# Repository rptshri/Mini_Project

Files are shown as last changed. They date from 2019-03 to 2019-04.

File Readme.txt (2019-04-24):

http://www.me.umn.edu/education/undergraduate/writing/How-to-write-a-Design-Report.pdf

ARDUINO DESIGN:
https://www.allaboutcircuits.com/technical-articles/understanding-arduino-uno-hardware-design/

SG90 http://www.ee.ic.ac.uk/pcheung/teaching/DE1_EE/stores/sg90_datasheet.pdf

MG995 https://www.towerpro.com.tw/product/mg995/

BLUETOOTH MODULE  https://howtomechatronics.com/tutorials/arduino/arduino-and-hc-05-bluetooth-module-tutorial/

MDF https://en.wikipedia.org/wiki/Medium-density_fibreboard

3D Design https://www.tinkercad.com/things/dJmnHaHhOIF-grand-snaget-amur/edit

Materials https://www.3dhubs.com/knowledge-base/pla-vs-abs-whats-difference 

MDF Plywood difference https://www.livspace.com/magazine/mdf-vs-plywood-comparison/

1. Project report *
2. Imperial Sheet *
3. Project hardware  *   
4. Project log book *
5. altium pcb file 
6. Proteus simulation file *
7. Pcb vs schematic.  8.Code

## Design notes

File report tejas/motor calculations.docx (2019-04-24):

Mass of robot = 1.5 KG

Radius of wheel = 5.5 cm = 0.055 m

Torque required = m*g*R

Where -

m= mass of robot

G= gravity

R=radius of wheel

Therefore

Torque = 1.5*9.8*0.055

=0.8085 N.M

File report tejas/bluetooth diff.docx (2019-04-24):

parameter | Hc-05 | Hc10
Bluetooth version | BLE 2.0/3.0 | BLE4.0
Power consumption | Low | Very Low
cost | Rs 283 /- | Rs 342 /-

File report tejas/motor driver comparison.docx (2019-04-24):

MOTOR DRIVER COMPARISON

Parameter | L293d | L298n
Circuit | Quadruple half bridge | Dual full H bridge
Supply voltage range | 4.5-36v | Upto 46 v
Output current | 600 mA | 2 A
Noise immunity | High | High
Over-temperature protection | NO | YES
Internal ESD protection | YES | NO
Cost | Low | Comparatively cost
Current Sense | No | Yes

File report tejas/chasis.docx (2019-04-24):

Chasis

Chasis is internal vehicle frame that provides base and supports an artificial object in its construction and use ,it also provides protection for some internal parts.

metal plates,fiber,or MDF materials can be used to make the chasis.

Metal plates are hard to work with. Cutting ,drilling, and welding requires special tools & too much efforts.

But MDF can be cut using normal hack-saw blade , and drilling can also be done easily.

So we used MDF material (Medium Density Fibreboard) to make the chasis.

Medium-density fibreboard (MDF) is a wood product made by breaking down hardwood or softwood residuals into wood fibres, often in a defibrator, combining it with wax and a resin binder, and forming panels by applying high temperature and pressure. MDF is generally denser than plywood.

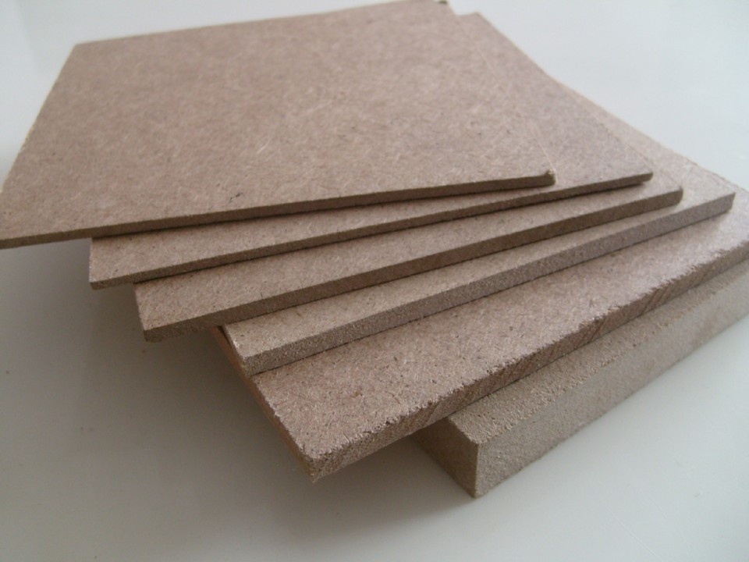
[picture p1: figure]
Image result for mdf material

MDF is typically made up of 82% wood fibre (https://en.wikipedia.org/wiki/Wood_fibre), 9% urea-formaldehyde (https://en.wikipedia.org/wiki/Urea-formaldehyde) resin glue, 8% water and 1% paraffin wax (https://en.wikipedia.org/wiki/Paraffin_wax).

We chosen this material because of advantages like light weight and ease of use.

Screws

We used M3 mounting screws to assemble the chasis . we made 3 compartments for battery pack,controller and motor driver,

Reference

MDF https://en.wikipedia.org/wiki/Medium-density_fibreboard

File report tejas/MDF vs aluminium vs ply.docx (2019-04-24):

MDF vs aluminium

| Aluminium Sheet | MDF | Plywood
cost | High | Low | Moderate
Cutting and drilling | Not easy | Can be cut with hand easily | Not easy
weight | High | Low | Moderate
Water resistance | No dominant effect of water | It soaks water and swells | It also soaks water slowly
safety | Hazardous due to sharp edges | Safe | Safe

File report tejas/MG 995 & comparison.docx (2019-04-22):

SERVO MG995

This high-speed standard servo can rotate approximately d120 degrees (60 in each direction). And we need only 45degree rotaion for the robotic arm to completely open and close.

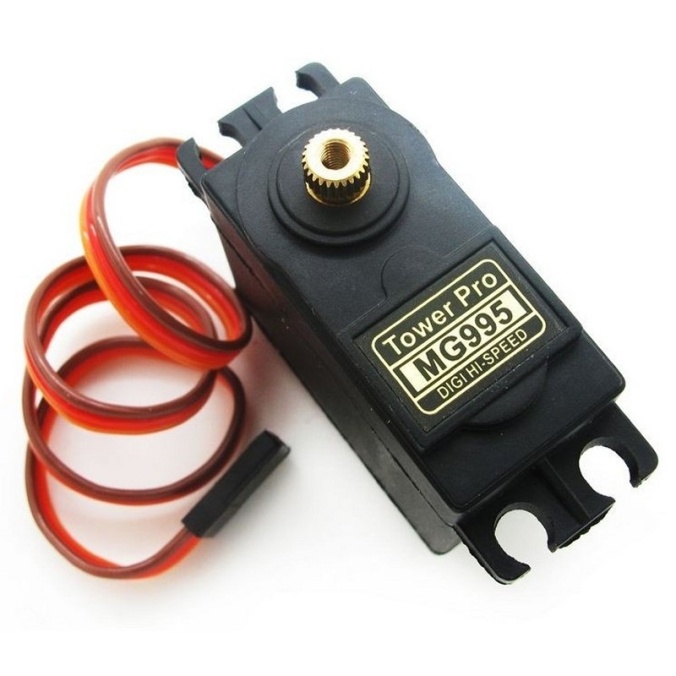
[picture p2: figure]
Image result for mg 995
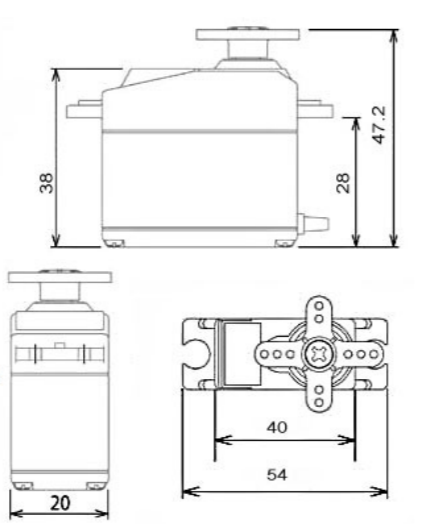
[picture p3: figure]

Specifications

• Weight: 55 g

• Dimension: 40.7 x 19.7 x 42.9 mm approx.

• Stall torque: 8.5 kgf·cm (4.8 V ), 10 kgf·cm (6 V)

• Operating speed: 0.2 s/60º (4.8 V), 0.16 s/60º (6 V)

• Operating voltage: 4.8 V a 7.2 V

• Dead band width: 5 µs

• Stable and shock proof double ball bearing design

• Temperature range: 0 ºC – 55 ºC

- Weight calculation

Torque given is 8.5 kg-cm for 4.8v supply

Means it can lift upto 8.5 kg with 1 cm of shaft length

Our arm length is 8.5 cm

So

Maximum lifting weight = torque/arm length

=8.5/8.5

=1 kg

- Maximum arm opening is 11.3 cm ,so maximum holding length is 11.3cm .

It is supposed to hold objects of 2cm to 10 cm more precisely.

- Arm opening time

Speed given is 0.2 sec/60deg

Therefore for 45 degree rotation it will take

( 0.2)45/60= 0.15

It means arm will open or close in 150 msec (for full speed).

Comparison table

| SG90 | MG995
Input | PWM | PWM
voltage | 4.8v-5v | 4.8v-7.2v
Rotation angle | 360 degree | 120 degree
Maximum torque | 1 KG | 8.5 KG
Max lifting weight with 8.5cm shaft | 294 Grams | 1000 Grams
Arm opening time | 12.5 msec | 150 msec
Weight | 14.7 g | 55 g
Dimensions | 32 x 12 x 32 mm | 40.7 x 19.7 x 42.9 mm

Reference https://www.towerpro.com.tw/product/mg995/

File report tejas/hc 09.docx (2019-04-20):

Bluetooth module HC09

A communication interface is necessary for the robot to convey location information. We are using Bluetooth module hc-09 (having Bluetooth 4.1 technology).

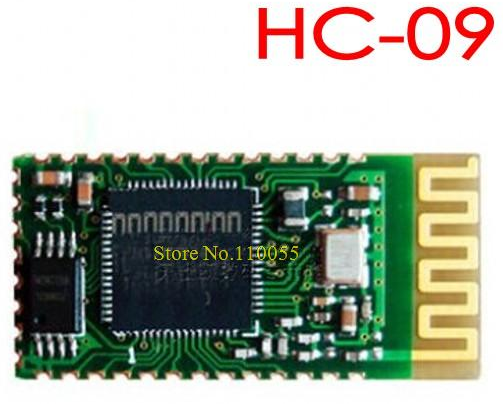
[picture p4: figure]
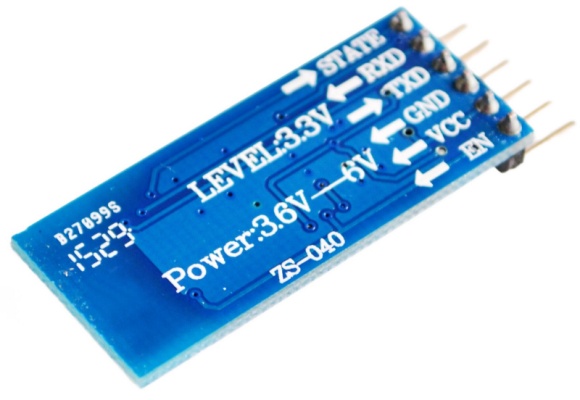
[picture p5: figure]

Feature:
1, serial module operating voltage 3.3V.
2, the baud rate can be set 2400,4800,9600,19200,38400,57600,115200,230400
3 core module size: 28mm x 15 mm x 2.35mm.

The module has 6 pins

PIN | FUNCTION
State | Gives status about connection
RXD | Reveive pin
TXD | Transmit pin
GND | Ground
VCC | +3.3 v input
EN | Enable pin

A mobile phone will communicate to bot controller (atmega 328p) through Bluetooth module. Phone will send data over Bluetooth to the module. And module will send data serially to the controller.

Testing

- For testing purpose , we interfaced Bluetooth module to the arduino UNO board. And wrote a program to display the received data on computer screen
- We selected alphabets A to G as valid data and all other characters, signs, spaces & special characters as invalid data.
- We have pin0 and pin1 of UNO board as RX and TX respectively, that we are using for sending the received data on computer.
- So we used pins 8 and 9 to interface Bluetooth module. A function called SoftwareSerial
- Configures the normal GPIO pins as TX and RX for serial communication.
- Data transmitted through Mobile phone via app “serial Bluetooth terminal “ .
- Arduino has inbuild LED connected on pin 13. We used that LED to indicate that valid data is received.

Connection chart

HC-09 | Arduino UNO
State | Nc
RXD | D9
TXD | D8
GND | Gnd
VCC | +3.3v
EN | +5v

Program

#include <SoftwareSerial.h>

#define LED_PIN 13

SoftwareSerial mySerial(8, 9); // RX, TX for arduino

// Connect HM10 Arduino Uno

// Pin 1/TXD Pin 8

// Pin 2/RXD Pin 9

void setup()

{ Serial.begin(9600); //9600 baudrate

pinMode(13, OUTPUT);

mySerial.begin(9600); //bluetooth module supports 9600 baudrate

mySerial.println("welcome "); //send message welcome to phone

}

void loop()

{char c;

if (mySerial.available()) //if there is data on the line

{

c = mySerial.read(); //copy data in variable c

if (c != '0' && c != '\n' && c != '\r' && c != ' ')

//to ignore non-character inputs

{ delay(1);

Serial.println("char received");

}

/* Here onwards compare the received data to valid inputs (A-G) and transmit the same on serial monitor*/

if (c == 'a' || c == 'A')

{

Serial.println("A received"); led();

}

else if (c == 'b' || c == 'B')

{

Serial.println("B received"); led();

}

else if (c == 'c' || c == 'C')

{

Serial.println("C received"); led();

}

else if (c == 'd' || c == 'D')

{

Serial.println("D received"); led();

}

else if (c == 'E' || c == 'e')

{

Serial.println("E received"); led();

}

else if (c == 'F' || c == 'f')

{

Serial.println("f received"); led();

}

else if (c == 'g' || c == 'G')

{

Serial.println("G received"); led();

}

/* now if received data is invalid, then send message “invalid input !” to serial terminal and mobile phone. */

if ((c >= 14 && c <= 64) || (c >= 73 && c <= 96) || (c >= 104))

{

Serial.println("Invalid Input!");

mySerial.println("Invalid Input!");

}

}

}

/* function to flash inbuilt LED (5 times) on receiving valid data */

void led()

{ int i;

for (i = 0; i < 5; i++)

{ digitalWrite(LED_PIN, HIGH);

delay(50);

digitalWrite(LED_PIN, LOW);

delay(50);

}

}

Reference

Testing https://howtomechatronics.com/tutorials/arduino/arduino-and-hc-05-bluetooth-module-tutorial/

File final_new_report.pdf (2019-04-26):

SWCPPR

BansilalRamnathAgarwal Charitable Trust’s

## Vishwakarma Institute of Information Technology

## (Department of Electronics & Telecommunication)

A

### Project entitled

## “Smart Wireless Controlled Pick-N-Place Line Following Robot”

### Submitted by

Arpit Shrivastava (T150393199) Durgesh Vitore (T150393219) Tejas Shinde (T150393196)

Employability Skills and Mini Project

T.E. Electronics & Tele-Communication

of

University of Pune

Under the supervision of

(Dr.S.R.Joshi)

Year 2018 – 2019

BansilalRamnathAgarwal Charitable Trust’s

## Vishwakarma Institute of Information Technology

## (Department of Electronics & Telecommunication)

CERTIFICATE

This is to certify that the project “Smart Wireless Controlled Pick N Place Line Following Robot” has been successfully completed by

Arpit Shrivastava
Durgesh Vitore
Tejas Shinde

It is a work done by the students and has not been submitted previously by any other student/students.

The work is done, on the basis of the work allotted to these students, based on various Project ideas presented by them.

This project report is being submitted as a part of the subject Mini Project and Seminar at T.E.-E&TC

(Dr.S.R.Joshi) | (Dr.S.V.Kulkarni)
Project Guide | H.O.D- E& TC

## ACKNOWLEDGEMENT

The ‘Smart Wireless Pick and Place Robot’ designed and develop by us is

a small effort in taking a step towards automation in day to day life things.

At first, we would like to express our sincere gratitude to our project guide

Dr.S.R.Joshi for Motivating us to implement such idea and also keeping us on track

throughout the project by providing constant guidance and all the support we required to

complete the project.

We are also grateful and indebted to Dr.S.V.Kulkarni for constantly putting

efforts to enhance our skills and required knowledge about various aspects that are

required for making a successful project.

We are also thankful to entire teaching and non-teaching staff of the electronics

and Telecommunication Department.

Last but not the least we would like to thank each and every person who helped us

directly or indirectly to complete this project.

Arpit Shrivastava

Durgesh Vitore

Tejas Shinde

INDEX

Sr.

No

Contents | Page No.

### 1. INTRODUCTION:

Mankind has always struggled to find alternatives for himself to work in hostile zones

and carry out his orders. The popular concept for this is robot which is machine that

performs specific task according to orders given to it.

As next industrial revolution is upon us, as industry 4.0 brings a new wave of

connected manufacturer’s and smart factories. Industry 4.0 involves a combination of

automation and the IOT, which collectively create smart factory.

The modern industry is moving from automation towards “Robotization” to

maintain product quality and increase productivity. Today’s robots provide more and

more anthropomorphic structure and human capabilities in these.

Here how a pick and place robot can be designed for industries where store rooms

are to be managed or loading and packing is to be done. Various problems and

obstructions are taken into consideration and analysed taken into consideration while

designing the robot.

1.1 AIM AND OBJECTIVE:

The main objective of pick and place robot is picking the object form

source location and place it to desired destination. The mechanical arm is

arrangement made for picking and placing the object. For detection purpose

proximity sensors are used.

The robot is made of three sections. The top gripper unit is to pick and

place any object. The bottom driving unit is to move the object to location

specified by user. And control unit which will control the operation of whole

system.

In Short, this project is to design an autonomous robot with complete

system that allow the robot to identify predefined locations and interact with

desired object.

1.2 IMPORTANCE:

In today’s scenario, the industry having a problem by human life in some

hazardous duty service. Robots can work in hazardous environments where

unprotected human would quickly die.

### 2. BACKGROUND:

Automation as a technology is concerned with the use of mechanical,

electrical, electronic and computer-based control systems to replace human beings

with machines, not only for physical work but also for the development of

information processing. Industrial automation, which started in the eighteenth

century as fixed automation has transformed into flexible and programmable

automation in the last 15 or 20 years. Computer numerically controlled machine

tools, transfer and assembly lines are some examples in this category

Scientific interpretation of science fiction scenario propounds a robot as an

automatic machine that is able to interact with and modify the environment in

which it operates. Therefore, it is essential to define what constitutes a robot.

Different definitions from diverse sources are available for a robot.

Three laws of Robotics:

1. A robot should not injure a human being or, through inaction, allow a

human to be harmed.

2. A robot must obey orders given by humans except when that conflicts with

the First Law.

3. A robot must protect its own existence unless that conflicts with the First or

Second law.

For our project we decided to make a pick and place robot. Through the

literature survey we found basic principles of pick and place robots and many

associated problems that are needed to be solved.

Optimization of these robots is still very important field. main specifications of

pick and place robots are speed of operation, precision, maximum load, range of

motion and cost.

### 3. BLOCK DIAGRAM:

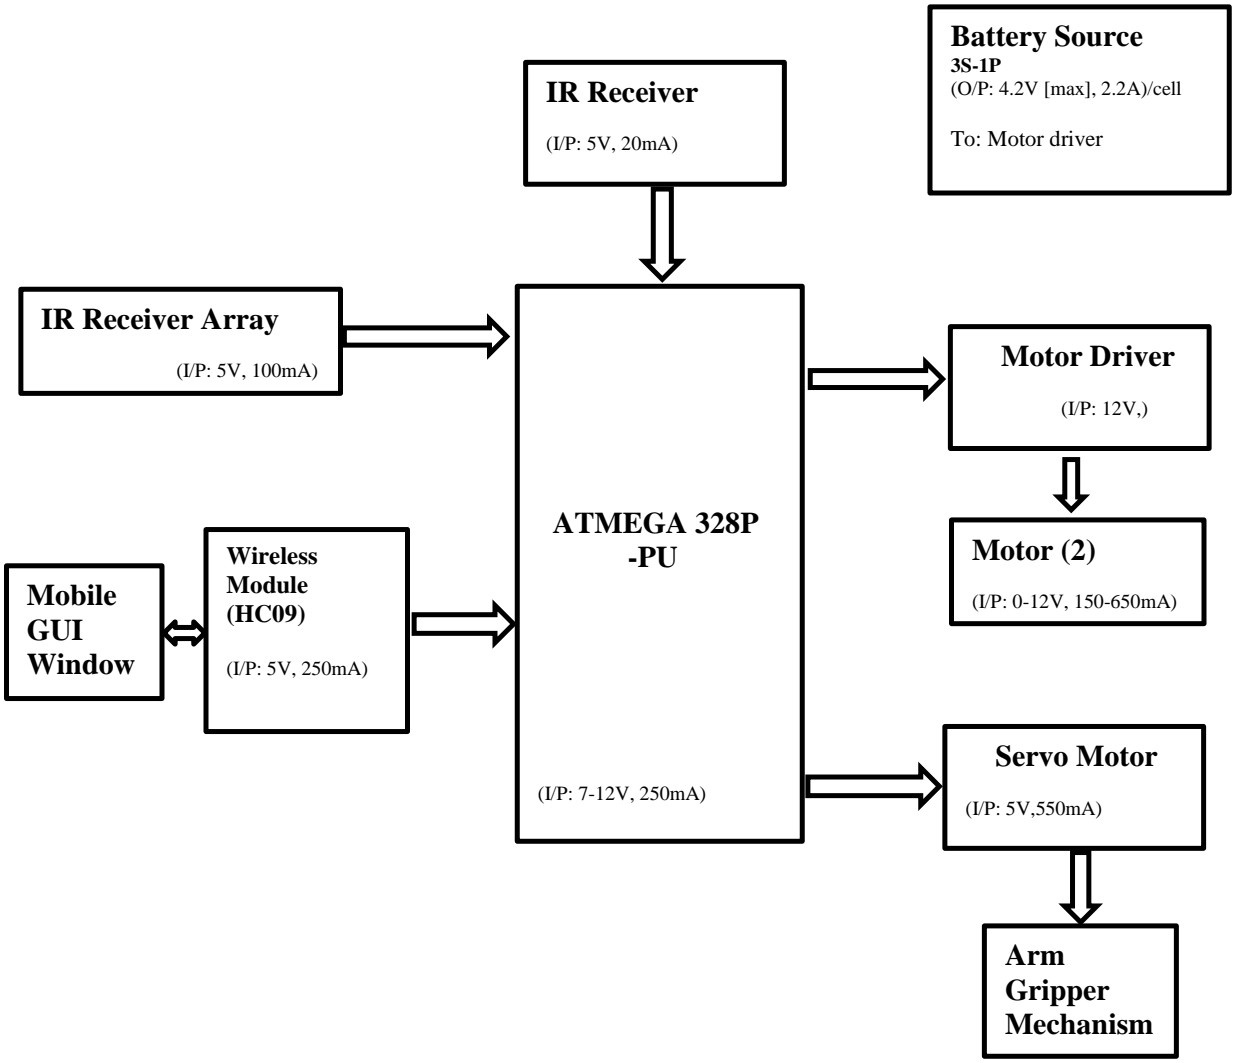
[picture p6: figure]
ATMEGA 328P -PU; IR Receiver; Motor Driver; Motor (2); IR Receiver Array; Mobile GUI Window; Wireless Module (HC09); Servo Motor; Battery Source; 3S-1P (O/P: 4.2V [max], 2.2A)/cell; To: Motor driver; Arm Gripper Mechanism

- Input and output devices: Wireless Module, Infrared Sensors, Motor Driver,

Servo Motors.

- Input device: Mobile app Bluetooth terminal.
- Mechanical devices: Gripper, Chassis.

### 4. ELECTRONIC AND HARDWARE DESIGN ASPECTS:

### 4.1 MICROCONTROLLER:

Microcontroller is necessary to read data provided by all sensors and to

provide instructions to the whole system. It controls movement of robot in the

direction provided by user with the help of Bluetooth module. It is the Brain of

Robot.

For this application, we are using ATMEGA328P-PU. The software which

we are using is Arduino IDE which is an open source software. The programmer

for ATMEGA328P-PU is also cheap.

PARAMETERS | PIC18F4550 | PIC16FXXX | ATMEGA328P-PU
CPU Speed (MIPS) | 12 | 5 | 20
Operating Frequency | 48MHz | 20MHz | 20MHz
RAM (bytes) | 2048 | 368 | 2048
CCP Module | 1 | 2 | 2
ADC | 13 Channel 10 bits | 8 Channel 10 Bit | 8 Channel 10 Bit
Operating Voltage | 2V-5.5V | 2V-5.5V | 1.8-5.5V
USB Support | Yes | No | N0
Price | 300 | 200 | 110

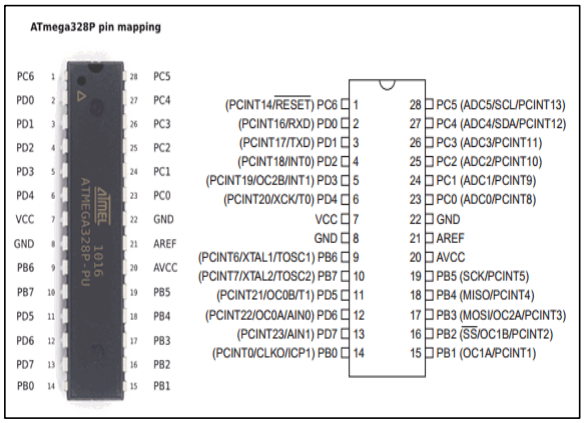
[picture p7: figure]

### 4.2 MOTOR DRIVER

L293D is dual H-bridge motor driver. Motor drivers act as current

amplifiers since they take low current control signal and provide a higher current

signal. This high current is used to drive the motors.

We designed our motor driver PCB by referring the L293D internal

structure.

Parameter | L293d | L298n
Circuit | Quadruple half bridge | Dual full H bridge
Supply voltage range | 4.5-36v | Up to 46 v
Output current | 600 mA | 2 A
Noise immunity | High | High
Over-temperature protection | NO | YES
Internal ESD protection | YES | NO
Cost | Low | Comparatively cost
Current Sense | No | Yes

L298N Motor
Driver

### 4.3 DC MOTOR:

DC motors for the movement of the robot. DC motors are connected to the

wheels of the robot. The speed and load shifting capacity of robot will depend

upon the RPM and Torque generated by the motors.

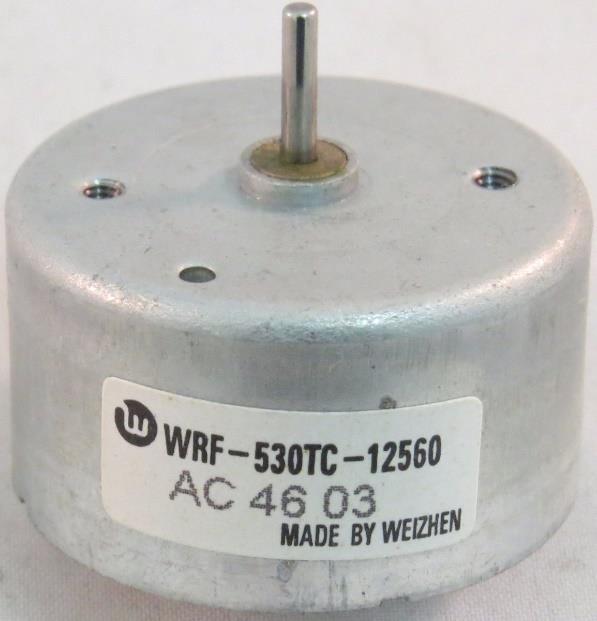
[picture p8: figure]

### 4.4 SERVO MOTOR SELECTION:

Features | SG90 | MG995
Input | PWM | PWM
voltage | 4.8v-5v | 4.8v-7.2v
Rotation angle | 360 degree | 120 degree
Maximum torque | 1 KG | 8.5 KG
Max lifting weight with 8.5cm shaft | 294 Grams | 1000 Grams
Arm opening time | 12.5 msec | 150 msec
Weight | 14.7 g | 55 g
Dimensions | 32 x 12 x 32 mm | 40.7 x 19.7 x 42.9 mm

Motor without
Gear Assembly

This high-speed standard servo can rotate approximately d120 degrees (60

in each direction). And we need only 45degree rotation for the robotic arm to

completely open and close.

Specifications

- Weight: 55 g
- Dimension: 40.7 x 19.7 x 42.9 mm approx.
- Stall torque: 8.5 kgf·cm (4.8 V), 10 kgf·cm (6 V)
- Operating speed: 0.2 s/60º (4.8 V), 0.16 s/60º (6 V)
- Operating voltage: 4.8 V a 7.2 V
- Dead band width: 5 µs
- Stable and shock proof double ball bearing design
- Temperature range: 0 ºC – 55 ºC.

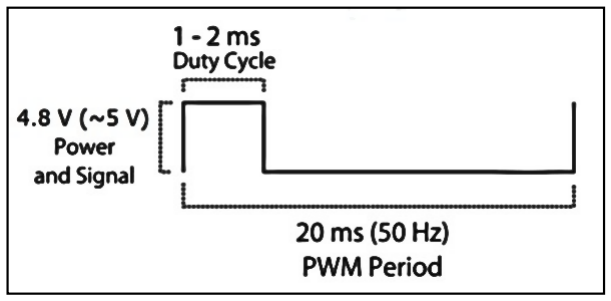
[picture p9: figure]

Pulse | Rotation angle
1ms | -90
1.5ms | 0
2ms | 90

### 4.5 BATTERY SOURCE SELECTION:

Lithium ion batteries have high energy density and cost less

than lithium polymer. Lithium polymer batteries are light weight and have

improved safety. However, their cost is high (30% average) as compared

to lithium ion.

Features | (18650 cells) Li-Ion | (Orange) Li-Po
Ageing | Loses actual charging capacity | Retains charging capacity better than Li-Ion
Energy Density | High Energy Density | Low as compared to Li-Ion
Conversion Rate | The capacity to convert battery into actual power 85-95% | 75-85%
Safety | More Volatile as compared to Li-Poly | More Safety, Less chance of explosion
Cost | Cheaper (200) | Slightly Expensive (+30%)
Weight | Heavier | Light Weight
Charge Duration | Longer Charge | Comparatively Shorter

We are using lithium-ion battery to power the robot. As Lithium-

ion batteries are rechargeable batteries and portable, with a high energy

density.

One cell will provide nearly 6Amperes of current. We are using 3 cells.

A Single 18650
cell.

### 4.6 BLUETOOTH MODULE (BM-10)

A communication interface is necessary for the robot to convey location information.

PARAMETERS | HC-05 | HC10
Bluetooth version | BLE 2.0/3.0 | BLE4.0
Power consumption | Low | Very Low
cost | Rs 283 /- | Rs 342 /-

We are using Bluetooth module BM-10 (having Bluetooth 4.1 technology).

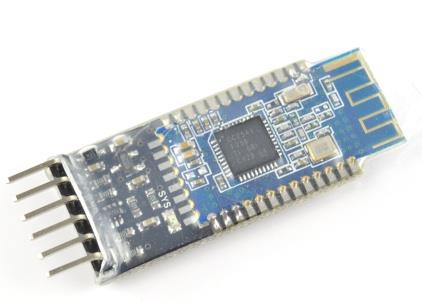
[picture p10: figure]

### 4.7 ROBOT ARM

A robotic arm is a type of mechanical arm. Which can perform near similar to

human arm. Our robotic arm is specially designed by us for pick and place

type task. It is designed by online 3D design software (TinkerCad). And

made using 3D printing technology.

- 3D DESIGN:

We tried various shapes and sizes to obtain maximum grip as well as

high strength. Previously we finalized ‘F’ shaped arms with 4 teeth on each

arm. But it would fail to hold round shaped objects.

So, we provided angles to arm & increased number of teeth so that it

would hold the multiple sides of object and get maximum grip.

BM10

Gears are also added so that whole arrangement can be moved using

single actuating element (servo motor).

This 3D structure is designed using an online software ‘TinkerCad’.

- 3D PRINTING:

To fabricate this 3D object, we used 3D printing technology. A special

machine called 3D printer can make this 3D structure. We have to provide

only 3D object file (.stl file) & select the amount of material to be filled.

3D printer is an expensive machine that wasn’t available with us. So, we

took help of a company ‘Infinity Systems’ to fabricate that structure.

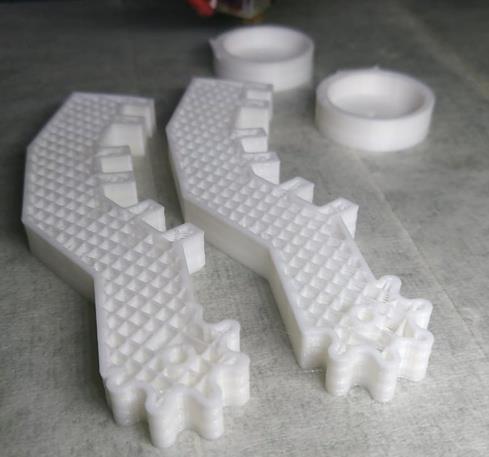
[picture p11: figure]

- MATERIAL USED:

Three type of materials can be used to print this object:

- HIPS (high impact polystyrene)
- ABS (Acrylonitrile Butadiene Styrene.)
- PLA (polylactic acid).

HIPS is costly material with not so considerable features.

ABS (http://amzn.to/2mdb53v) is widely available (http://amzn.to/2mdb53v) and has been a very popular plastic in the

development of prosumer 3D printing from the start. It melts consistently at

around 225 degrees Celsius, which can easily be achieved with small and home-

safe electronics.

PLA (http://amzn.to/2lXFQJg) is made from corn starch or sugar cane and is biodegradable, so it’s more

environmentally-friendly than ABS. It melts can melt at a lower temperature

between 190 and 210 degrees and doesn’t smell bad when it does.

PLA also has high tensile strength(37Mpa) than ABS (27Mpa).

So, by looking at these advantages we chosen PLA for our application. Because

of high strength Only 25% fill of PLA can satisfy the application need.

Robot Arm
while being
printed.

### 4.8 CHASSIS DESIGN:

Chassis is internal vehicle frame that provides base and supports an artificial

object in its construction and use, it also provides protection for some internal parts.

Metal plates, fibre, or MDF can be used to make Chassis.

Metal plates are hard to work with. Cutting, drilling, and welding requires special tools &

too much efforts. But MDF can be cut using normal hack-saw blade, and drilling can

also be done easily.

Features | Aluminium Sheet | MDF | Plywood
Cost | High | Low | Moderate
Cutting and drilling | Not easy | Can be cut with hand easily | Not easy
Weight | High | Low | Moderate
Water resistance | No dominant effect of water | It soaks water and swells | It also soaks water slowly
Safety | Hazardous due to sharp edges | Safe | Safe

So, we used MDF material (Medium Density Fibreboard) to make the chassis.

Medium-density fibreboard (MDF) is a wood product made by breaking down hardwood

or softwood residuals into wood fibres, often in a defibrator, combining it with wax and

a resin binder, and forming panels by applying high temperature and pressure. MDF is

generally denser than plywood.

We chose this material because of advantages like light weight and ease of use

MDF is typically made up of 82% Woodfibre, 9%

urea-formaldehyde resin glue, 8% water and

1% paraffin-wax.

### 5. SOFTWARE ASPECTS:

### 5.1 KICAD: -

- This software is used for PCB Designing
- We have designed a controller board for ATMEGA 328P-PU and Motor

driver using L298N using KICAD.

- First, we made a schematic for these boards and then updated PCBs from

schematic by assigning them appropriate footprints.

### 5.2 ARDUINO IDE: -

- Arduino IDE is used for microcontroller programming
- Program consists of programming for Motors, Sensors and Motor driver,

Servo Motor.

### 5.3 PROTEUS: -

- This software is used for simulation purpose
- We have performed simulation of this Smart Wireless controlled Pick-N-

Place Line Following Robot circuitry in order to check whether it is working

or not.

### 5.4 TIKERCAD: -

- TinkerCad is a free, easy-to-use app for 3D design, electronics, and

coding. It's used by teachers, kids, hobbyists, and designers to imagine,

design, and make anything!

- After Designing 3D Model, the STL File is exported and processed with

Slicing Software.

### 6. CIRCUIT DESIGN:

### 6.1 MICROCONTROLLER BOARD:

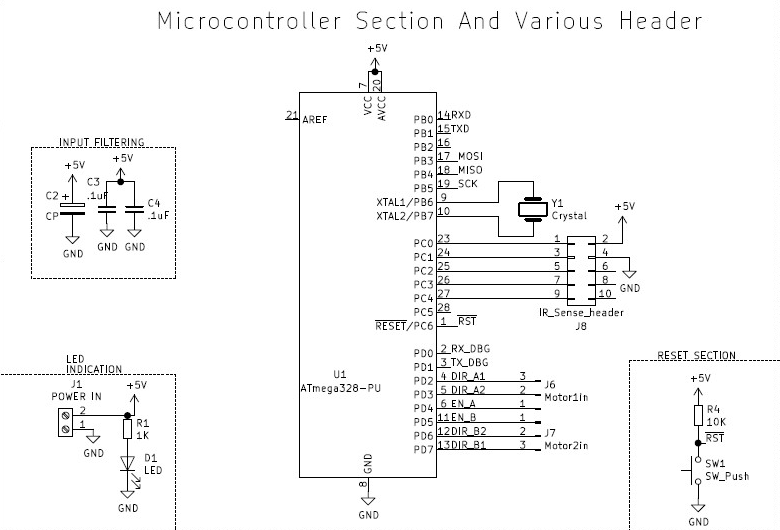
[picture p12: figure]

- 10KOhm resistor on reset pin to avoid accidental resetting of microcontroller
- Switch SW1 for Resetting Circuitry.
- C1, C4, C5 capacitors for filtering supply noise, gives high frequency noise signals low impedance path to ground (0.1 uF is the most common capacitor value). As Xc=1/(2πfC), more is Frequency lesser is Reluctance.
- ISP header for using external programmer using SPI protocol
- 16 MHz crystal for clock
- LED and 1K Resistor to Indicate Power.

### 6.2 MOTOR DRIVER (L298N):

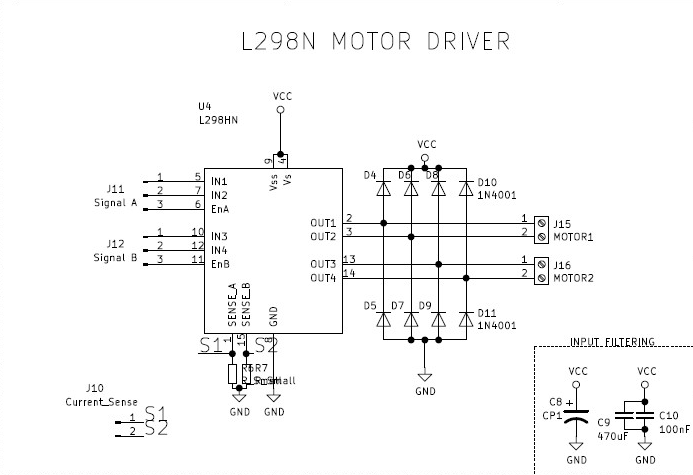
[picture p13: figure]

- Max Power 25W.
- Instantaneous Peak Current 3A.
- R6, R7=0Ω(ohm), as we are not using Current Sense.
- Logic Supply of 7V Max.
- 100nF Non-Inductive Capacitor And must be placed as near as possible to GND.
•
6.3 3.3V_REGULATION(AMS1117)
- Cp = 22uF to ensure stable voltage in all operating conditions.

6.4 5V_REGULATION (IC7805):

Provides 5V for Arduino Board and Servo Motor.

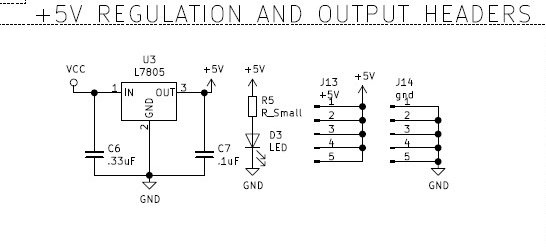
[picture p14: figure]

- C6 = 0.33uF for filtering input supply Noise.
- C7 = 0.1uF for filtering Output Supply, to ensued stability in all operating Conditions.

### 6.5 MOTOR CALCULATIONS:

Mass of robot = 1.5 KG

Radius of wheel = 5.5 cm = 0.055 m

Torque required = m*g*R | Where -
| m= mass of robot
| G= gravity
| R=radius of wheel

Therefore

Torque = 1.5*9.8*0.055

=0.8085 N.M

### 6.6 SERVO CALCULATIONS:

The servo motor is coupled to one of the arm of robotic arm, & to open the arm fully we

need only 45 degree rotation .So

Duty cycle= 1.5+(angle of rotation in degrees /180)

=1.5+(45 /180)

=1.75 ms

- Weight calculation:

Torque given is 8.5 kg-cm for 4.8v supply

Means it can lift upto 8.5 kg with 1 cm of shaft length

Our arm length is 8.5 cm. So,

Maximum lifting weight = torque/arm length

=8.5/8.5

=1 kg

- Maximum arm opening is 11.3 cm ,so maximum holding length is 11.3cm .

It is supposed to hold objects of 2cm to 10 cm more precisely.

- Arm opening time:

Speed given is 0.2 sec/60deg

Therefore for 45 degree rotation it will take

( 0.2) 45/60= 0.15

It means arm will open or close in 150 msec (for full speed).

### 7. SIMULATION RESULTS:

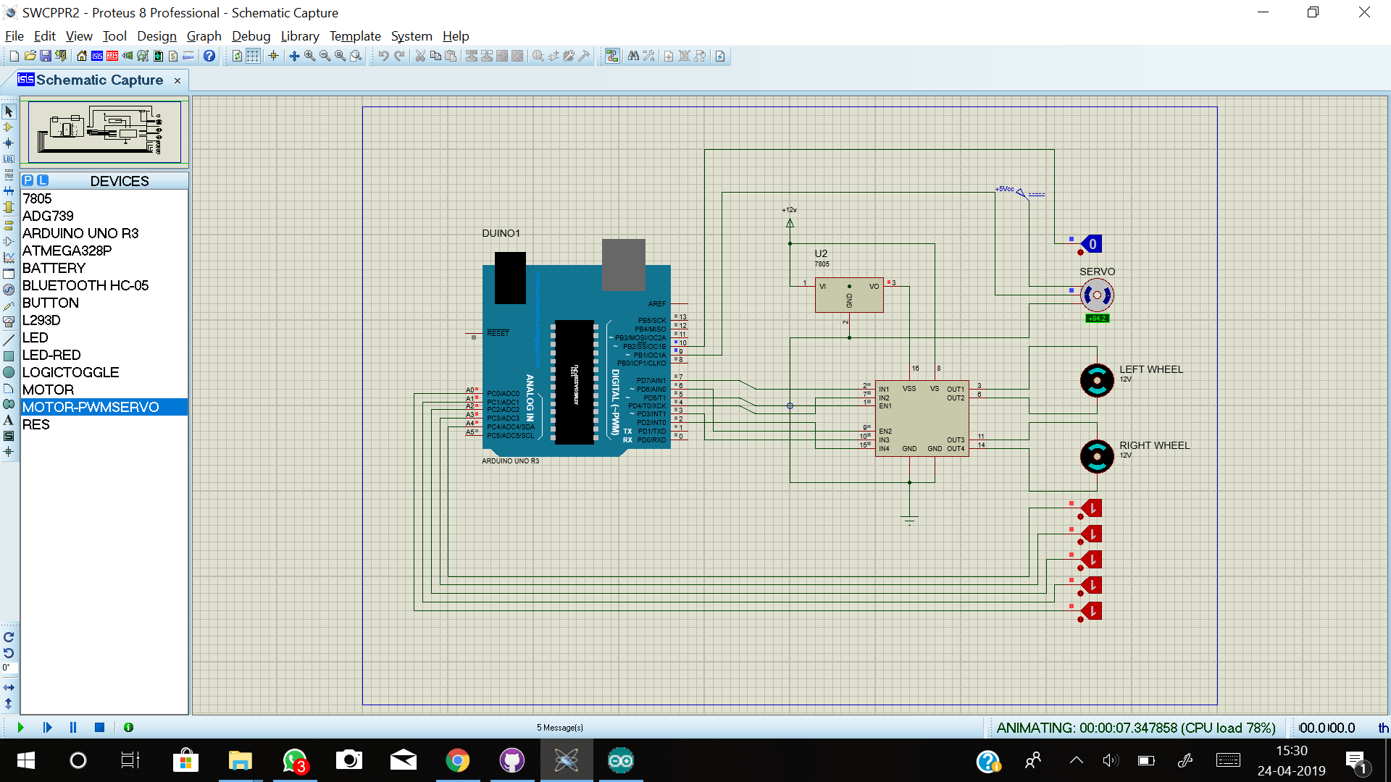
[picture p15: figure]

### - In place of IR Sensor, Switches are used to simulate the

conditions outcomes on Black over Right Line stripes.

### - The Motor speed and directions vary according to the

conditions written in the code.

- The servo motor is operated when the object is detected.

### 8. PCB LAYOUTS:

### 8.1 MICROCONTROLLER BOARD:

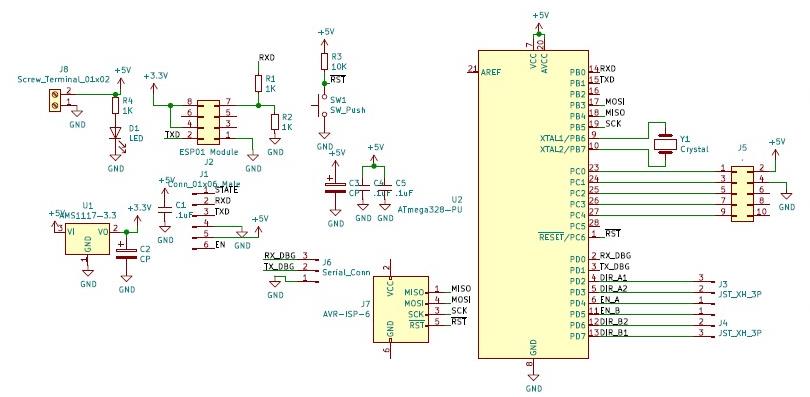
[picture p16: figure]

SCHEMATIC DIAGRAM

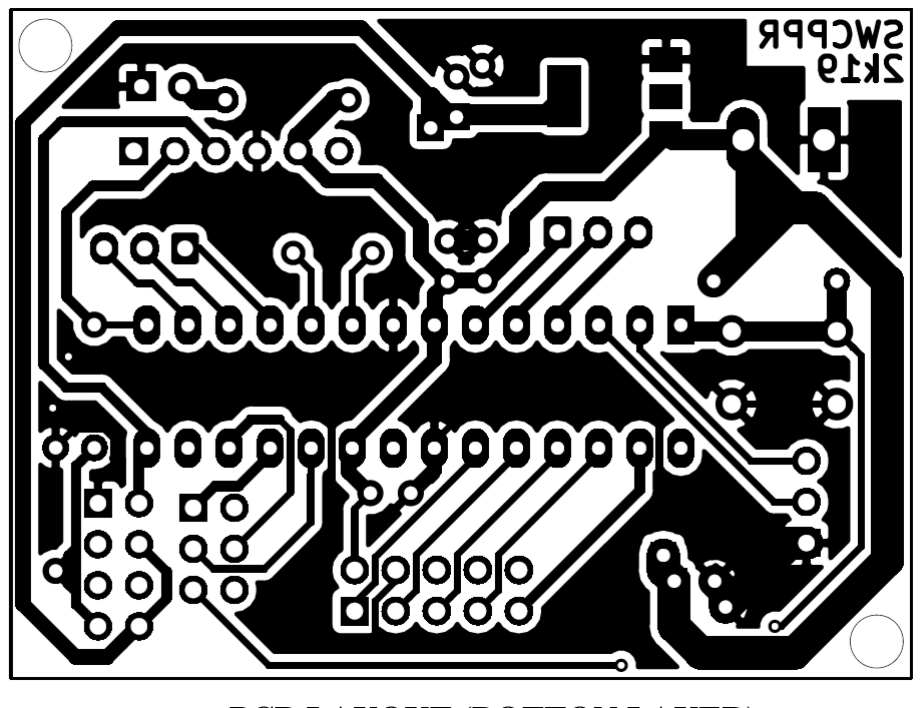
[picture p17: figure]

PCB LAYOUT (BOTTON LAYER)

### 8.2 MOTOR DRIVER BOARD:

SCHEMATIC DIAGRAM

PCB LAYOUT (BOTTON LAYER)

### 9. TESTING OF MODULES:

### 9.1 MOTOR DRIVER L298N:

Testing is done to ensure proper functionality of the circuits. Individual circuits &

modules should be tested separately so that there will not be any problems in

further design.

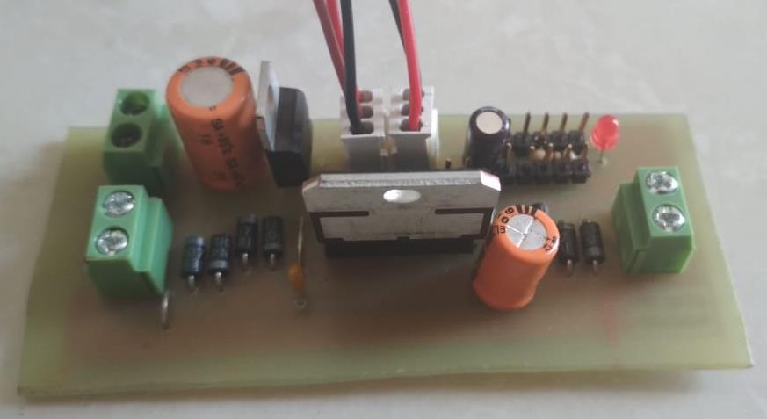
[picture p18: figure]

(top)

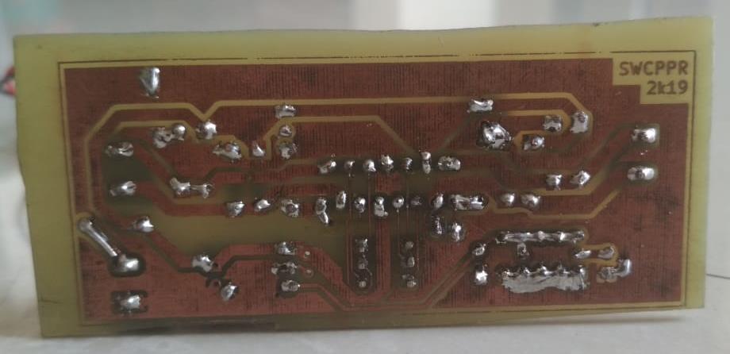
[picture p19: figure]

(BOTTOM)

L298 Board after soldering (2 channel)
We tested the board in 3 steps
- Component test

We checked that, all the components are in place & soldered properly or not.

- Continuity test
- By using DMM we checked the continuity of tracks to ensure the proper

conduction of the circuit.

- Some points that are supposed to be isolated but get connected by mistake

are also found out by continuity test.

- Functionality test
- In this step we check the actual operation of the circuit.
- This includes applying input and checking weather circuit is giving proper

output or not.

- We gave control signals using 5v & GND headers on the board and checked

the output voltage using DMM.

- Output voltage should be positive for clockwise and negative for counter-

clockwise direction.

- We performed this test for both the channels & got proper output.

### 9.2 MICROCONTROLLER BOARD:

We tested the board in 3 steps

- Component test

We checked that, all the components are in place & soldered properly or not.

- Continuity test
- By using DMM we checked the continuity of tracks to ensure the proper

conduction of the circuit.

- Some points that are supposed to be isolated but get connected by mistake

are also found out by continuity test.

- Functionality test
- In this step we check the actual operation of the circuit.
- This includes applying input and checking weather circuit is giving proper

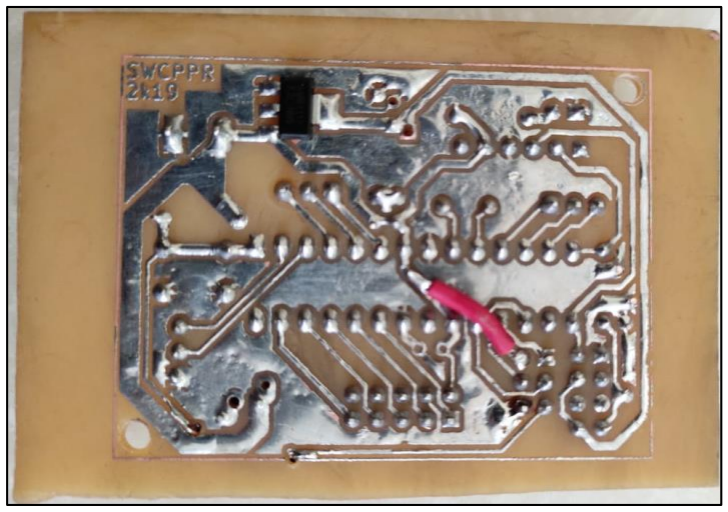
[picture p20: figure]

output or not

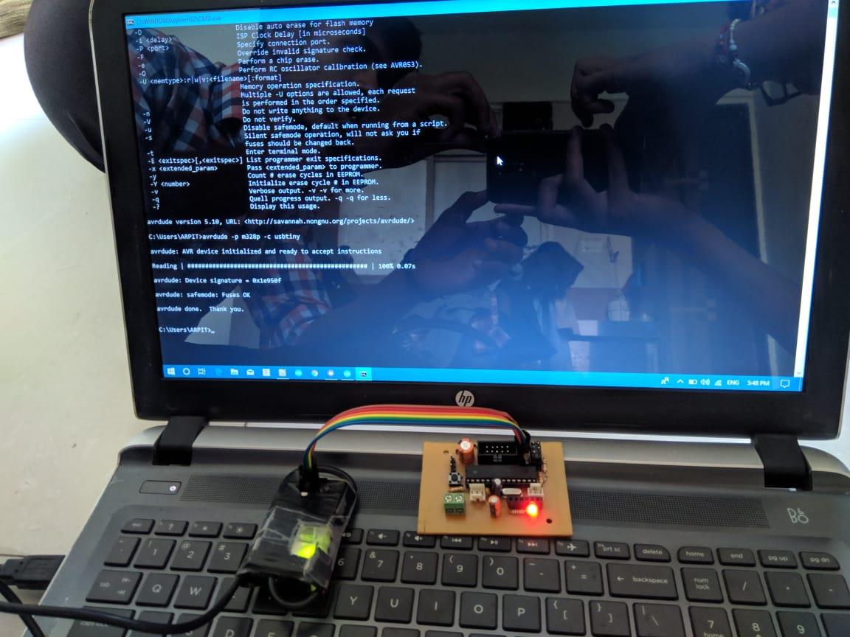
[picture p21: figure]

### 9.3 HC-09 BLUETOOTH MODULE:

We tested the board in following steps:

- For testing purpose, we interfaced Bluetooth module to the Arduino UNO

board. And wrote a program to display the received data on computer

screen

- We selected alphabets A to G as valid data and all other characters, signs,

spaces & special characters as invalid data.

- We have pin0 and pin1 of UNO board as RX and TX respectively, that we

are using for sending the received data on computer.

- So, we used pins 8 and 9 to interface Bluetooth module. A function called

SoftwareSerial

- Configures the normal GPIO pins as TX and RX for serial

communication.

- Data transmitted through Mobile phone via app Serial Bluetooth terminal
- Arduino has inbuild LED connected on pin 13. We used that LED to

indicate that valid data is received.

-Testing Working of Board
using “avrdude”

- Connection chart
HC-09 | Arduino UNO
State | Nc
RXD | D9
TXD | D8
GND | Gnd

### 9.4 SERVO MOTOR:

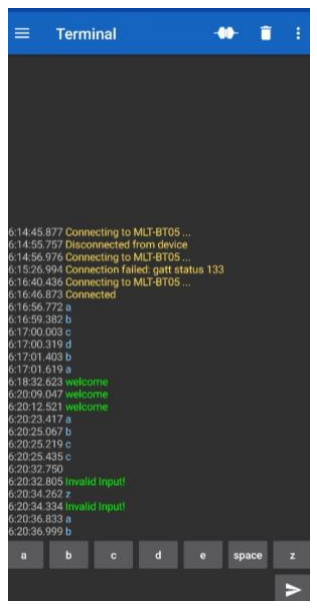
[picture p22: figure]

As discussed before, Testing is done to ensure proper functionality of the circuits.

Individual circuits & modules should be tested separately so that there will not be any

problems in further design.

For Servo motor we performed only functionality test because it is a ready-made device

& its internal circuits are not easily accessible.

Testing Servo motor requires PWM signal for its operation. Duty cycle of this input

signal decides the angle of rotation of the shaft.

For testing purpose, we interfaced the motor with Arduino UNO (PIN 3).

-Snap of Mobile App and Serial Terminal

And wrote a program to rotate the motor in both directions.

Connections: -

Servo pins | Arduino Uno pins
PWM | PIN 3
VCC | +5V
GND | GND

Program
#include <Servo.h> | // Include Servo library

int servoPin = 3; | // Declare the Servo pin
Servo Servo1; | // Create a servo object
void setup()
{
Servo1.attach(servoPin); // define pin 3 for servo1 }
void loop()
{
Servo1.write(0); // go to 0 degrees delay(1000);
Servo1.write(90); // go to 90 degrees delay(1000);
Servo1.write(180); // go to 180 degrees delay(1000);

}

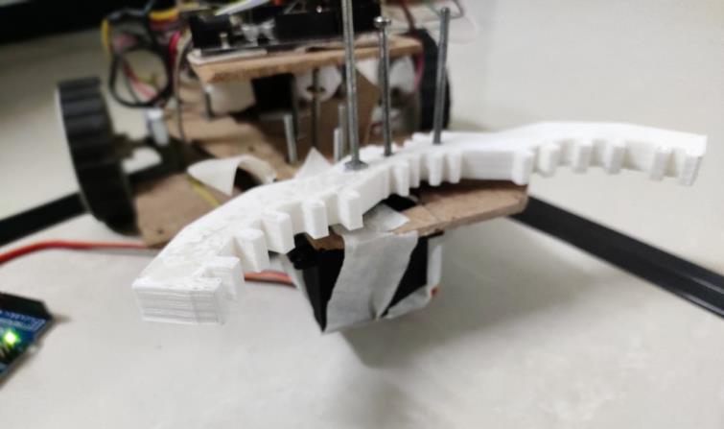
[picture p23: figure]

### 9.5 INFRARED MODULE:

- We used IR sensor array for line sensing. It is array of five IR sensors with 5 digital outputs.
- It gives 0 & 1 signals for black and white colour respectively.
- We performed functionality test for this module.
- By interfacing the IR array to Arduino Uno board, we transmitted the signal on serial terminal of pc.
- And checked the outputs by moving the sensor array on black and white backgrounds.

Connections
IR module | Arduino Uno
Sensor1 | 8
Sensor2 | 9
Sensor3 | 10
Sensor4 | 11
Sensor5 | 12
VCC | +5V
GND | GND

Test program
const int mod1 = 8;
const int mod2 = 9;
const int mod3 = 10;
const int mod4 = 11;

const int mod5 = 12;
unsigned long int val = 0b00000000; //variable to store Sensor data

void serialprint()
{
Serial.println(PINB, BIN); Serial.println("_______________________"); }
void setup()
{
Serial.begin(9600); | //set baudrate 9600
DDRB = 0x00; | // make port B as output
delay(1000);
}

void loop()
{
serialprint(); | //send sensor values on serial terminal
uint8_t val = PINB; | //copy the sensor values in a variable
}

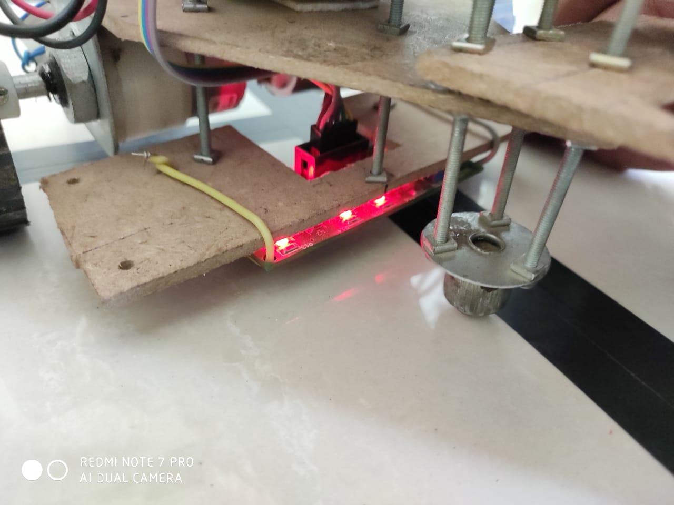
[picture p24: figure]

-IR Sensor testing with Black line on White Background.


### 10. CABINET DESIGN AND ASSEMBLY:


11.BILL OF MATERIALS:

Sr. No | Component Name | Value | Quantity | Amount
1 | PCB Manufacturing (Acetone, Copper clad, FeCl3, Safety Gloves,) | | 2 | 200₹
2 | ATmega328-PU | 28pin DIP | 1 | 125₹
3 | AMS1117-3.3 | SOT-23 | 1 | 5₹
4 | L298HN | TO-220(15) | 1 | 110₹
5 | L7805 | TO-220(3) | 1 | 10₹
6 | Crystal HC18-U | 16MHz | 1 | 4₹
7 | Resistor THT | 10K, 1K | 4 | 1₹
8 | Capacitor Disc THT | 1uF | 4 | 2₹
9 | LED | 3.5mm | 2 | 6₹
10 | JST Connection Header | 3pin male | 3 | 16₹
11 | Motor | (wrf-530Tc-12560) | 1 | 300₹
12 | Diode 1N4001 | THT | 9 | 9₹
13 | Button Switch | 4pin | 1 | 10₹/piece
14 | Capacitor Disc THT | 100nF, 470uF,.33uF | 1 | 9₹
15 | Connection Header Male | 2.54pitch | 1 | 6₹
16 | Connection Header Female | 2.54pitch | 1 | 6₹
17 | Wheels | 6cm | 2 | 120₹
18 | Servo Motor | MG995 | 1 | 350₹
20 | Chassis (MDF, Motor hinges, Screws, nuts washers,) | | | 200₹

1489₹

Approximate Budget is 1500₹.

### 12. REFERENCES:

-ARDUINO DESIGN:https://www.allaboutcircuits.com/technic-alarticles/understanding-arduino-uno-hardware-design/ (https://www.allaboutcircuits.com/technic-alarticles/understanding-arduino-uno-hardware-design/)

-SG90: http://www.ee.ic.ac.uk/pcheung/teaching/DE1_EE/stores/sg90_datasheet.pdf

-MG995: https://www.towerpro.com.tw/product/mg995/

-BLUETOOTH MODULE: https://howtomechatronics.com/tutorials/arduino/arduino-and-hc-05-bluetooth-module-tutorial/ (https://howtomechatronics.com/tutorials/arduino/arduino-and-hc-05-bluetooth-module-tutorial/)

-MDF: https://en.wikipedia.org/wiki/Medium-density_fibreboard

-3D Design: https://www.tinkercad.com/things/dJmnHaHhOIF-grand-snaget-amur/edit

-Materials: https://www.3dhubs.com/knowledge-base/pla-vs-abs-whats-difference

-MDF Plywood : https://www.livspace.com/magazine/mdf-vs-plywood-comparison/


### 13. PROJECT PHOTO:

- Hardware:

-3d model of Mosfet Driver as Designed on KiCad

-3d model of Microcontroller Board as Designed on KiCad


-Drilling of Boards

-Etching of Boards

-Soldering of Boards


-MOSFET Driver after Soldering (Top side on left)

-Microcontroller Board after Soldering (Top side on left)

### 14. CONCLUSION:

The design and development of pick and place robot has been carried out. A

prototype was confirmed functional working of robot system. This system would make it

easier for human beings to pick and place the risk of handling suspicious objects, which

could be hazardous in its present environment and workplace. Complex and complicated

duties can be achieved faster and more accurately with this design.

A robotic arm is implemented using Atmega328P-PU in pick and place objects

more safely without incurring much damage. The robotic arm used here contains a soft

catching gripper, which safely handles the object. In the modern era, time and man power

are major constraints for the completion of a task.

By the use of product, the industrial activities and hazardous operations can be done

easily and safely in a short span of time. The use of soft catching gripper and low power

wireless communication technique like BLE (4.0) makes our system more effective when

compared to other systems. The developed system is capable of lifting only small

weights; by introducing high torque motor large weights can be picked. A wireless

camera can also be implemented to track the movement of the vehicle and thus it can be

used for defense purposes. The range is also a limitation here but it can be enhanced.

15.DATASHEETS:

-pto

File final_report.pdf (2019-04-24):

SWCPPR

BansilalRamnathAgarwal Charitable Trust’s

## Vishwakarma Institute of Information Technology

## (Department of Electronics & Telecommunication)

A

### Project entitled

## “Smart Wireless controlled Pick-N-Place Line Following Robot”

### Submitted by

Arpit Shrivastava (T150393199) Durgesh Vitore (T150393219) Tejas Shinde (T150393196)

Employability Skills and Mini Project

T.E. Electronics & Tele-Communication

of

University of Pune

Under the supervision of

(Dr.S.R.Joshi)

Year 2018 – 2019

BansilalRamnathAgarwal Charitable Trust’s

## Vishwakarma Institute of Information Technology

## (Department of Electronics & Telecommunication)

CERTIFICATE

This is to certify that the project “Smart Wireless Controlled Pick N Place Line Following Robot” has been successfully completed by

Arpit Shrivastava
Durgesh Vitore
Tejas Shinde

It is a work done by the students and has not been submitted previously by any other student/students.

The work is done, on the basis of the work allotted to these students, based on various Project ideas presented by them.

This project report is being submitted as a part of the subject Mini Project and Seminar at T.E.-E&TC

(Dr.S.R.Joshi) | (Dr.S.V.Kulkarni)
Project Guide | H.O.D- E& TC

## ACKNOWLEDGEMENT

The ‘Smart Wireless Pick and Place Robot’ designed and develop by us is

a small effort in taking a step towards automation in day to day life things.

At first, we would like to express our sincere gratitude to our project guide

Dr.S.R.Joshi for Motivating us to implement such idea and also keeping us on track

throughout the project by providing constant guidance and all the support we required to

complete the project.

We are also grateful and indebted to Dr.S.V.Kulkarni for constantly putting

efforts to enhance our skills and required knowledge about various aspects that are

required for making a successful project.

We are also thankful to entire teaching and non-teaching staff of the electronics

and Telecommunication Department.

Last but not the least we would like to thank each and every person who helped us

directly or indirectly to complete this project.

Arpit Shrivastava

Durgesh Vitore

Tejas Shinde

INDEX

Sr.

No

Contents | Page No.

### 1. INTRODUCTION:

Mankind has always struggled to find alternatives for himself to work in hostile zones

and carry out his orders. The popular concept for this is robot which is machine that

performs specific task according to orders given to it.

As next industrial revolution is upon us, as industry 4.0 brings a new wave of

connected manufacturer’s and smart factories. Industry 4.0 involves a combination of

automation and the IOT, which collectively create smart factory.

The modern industry is moving from automation towards “Robotization” to

maintain product quality and increase productivity. Today’s robots provide more and

more anthropomorphic structure and human capabilities in these.

Here how a pick and place robot can be designed for industries where store rooms

are to be managed or loading and packing is to be done. Various problems and

obstructions are taken into consideration and analysed taken into consideration while

designing the robot.

1.1 AIM AND OBJECTIVE:

The main objective of pick and place robot is picking the object form

source location and place it to desired destination. The mechanical arm is

arrangement made for picking and placing the object. For detection purpose

proximity sensors are used.

The robot is made of three sections. The top gripper unit is to pick and

place any object. The bottom driving unit is to move the object to location

specified by user. And control unit which will control the operation of whole

system.

In Short, this project is to design an autonomous robot with complete

system that allow the robot to identify predefined locations and interact with

desired object.

1.2 IMPORTANCE:

In today’s scenario, the industry having a problem by human life in some

hazardous duty service. Robots can work in hazardous environments where

unprotected human would quickly die.

### 2. BACKGROUND:

Automation as a technology is concerned with the use of mechanical,

electrical, electronic and computer-based control systems to replace human beings

with machines, not only for physical work but also for the development of

information processing. Industrial automation, which started in the eighteenth

century as fixed automation has transformed into flexible and programmable

automation in the last 15 or 20 years. Computer numerically controlled machine

tools, transfer and assembly lines are some examples in this category

Scientific interpretation of science fiction scenario propounds a robot as an

automatic machine that is able to interact with and modify the environment in

which it operates. Therefore, it is essential to define what constitutes a robot.

Different definitions from diverse sources are available for a robot.

Three laws of Robotics:

1. A robot should not injure a human being or, through inaction, allow a

human to be harmed.

2. A robot must obey orders given by humans except when that conflicts with

the First Law.

3. A robot must protect its own existence unless that conflicts with the First or

Second law.

For our project we decided to make a pick and place robot. Through the

literature survey we found basic principles of pick and place robots and many

associated problems that are needed to be solved.

Optimization of these robots is still very important field. main specifications of

pick and place robots are speed of operation, precision, maximum load, range of

motion and cost.

### 3. BLOCK DIAGRAM:

ATMEGA 328P -PU; IR Receiver; Motor Driver; Motor (2); IR Receiver Array; Mobile GUI Window; Wireless Module (HC09); Servo Motor; Battery Source; 3S-1P (O/P: 4.2V [max], 2.2A)/cell; To: Motor driver; Arm Gripper Mechanism

- Input and output devices: Wireless Module, Infrared Sensors, Motor Driver,

Servo Motors.

- Input device: Mobile app Bluetooth terminal.
- Mechanical devices: Gripper, Chassis.

### 4. ELECTRONIC AND HARDWARE DESIGN ASPECTS:

### 4.1 MICROCONTROLLER:

Microcontroller is necessary to read data provided by all sensors and to

provide instructions to the whole system. It controls movement of robot in the

direction provided by user with the help of Bluetooth module. It is the Brain of

Robot.

For this application, we are using ATMEGA328P-PU. The software which

we are using is Arduino IDE which is an open source software. The programmer

for ATMEGA328P-PU is also cheap.

PARAMETERS | PIC18F4550 | PIC16FXXX | ATMEGA328P-PU
CPU Speed (MIPS) | 12 | 5 | 20
Operating Frequency | 48MHz | 20MHz | 20MHz
RAM (bytes) | 2048 | 368 | 2048
CCP Module | 1 | 2 | 2
ADC | 13 Channel 10 bits | 8 Channel 10 Bit | 8 Channel 10 Bit
Operating Voltage | 2V-5.5V | 2V-5.5V | 1.8-5.5V
USB Support | Yes | No | N0
Price | 300 | 200 | 110


### 4.2 MOTOR DRIVER

L293D is dual H-bridge motor driver. Motor drivers act as current

amplifiers since they take low current control signal and provide a higher current

signal. This high current is used to drive the motors.

We designed our motor driver PCB by referring the L293D internal

structure.

Parameter | L293d | L298n
Circuit | Quadruple half bridge | Dual full H bridge
Supply voltage range | 4.5-36v | Up to 46 v
Output current | 600 mA | 2 A
Noise immunity | High | High
Over-temperature protection | NO | YES
Internal ESD protection | YES | NO
Cost | Low | Comparatively cost
Current Sense | No | Yes

### 4.3 DC MOTOR:

DC motors for the movement of the robot. DC motors are connected to the

wheels of the robot. The speed and load shifting capacity of robot will depend

upon the RPM and Torque generated by the motors.


### 4.4 SERVO MOTOR SELECTION:

Features | SG90 | MG995
Input | PWM | PWM
voltage | 4.8v-5v | 4.8v-7.2v
Rotation angle | 360 degree | 120 degree
Maximum torque | 1 KG | 8.5 KG
Max lifting weight with 8.5cm shaft | 294 Grams | 1000 Grams
Arm opening time | 12.5 msec | 150 msec
Weight | 14.7 g | 55 g
Dimensions | 32 x 12 x 32 mm | 40.7 x 19.7 x 42.9 mm

This high-speed standard servo can rotate approximately d120 degrees (60

in each direction). And we need only 45degree rotation for the robotic arm to

completely open and close.

Specifications

- Weight: 55 g
- Dimension: 40.7 x 19.7 x 42.9 mm approx.
- Stall torque: 8.5 kgf·cm (4.8 V), 10 kgf·cm (6 V)
- Operating speed: 0.2 s/60º (4.8 V), 0.16 s/60º (6 V)
- Operating voltage: 4.8 V a 7.2 V
- Dead band width: 5 µs
- Stable and shock proof double ball bearing design
- Temperature range: 0 ºC – 55 ºC.


Pulse | Rotation angle
1ms | -90
1.5ms | 0
2ms | 90

### 4.5 BATTERY SOURCE SELECTION:

Lithium ion batteries have high energy density and cost less

than lithium polymer. Lithium polymer batteries are light weight and have

improved safety. However, their cost is high (30% average) as compared

to lithium ion.

Features | (18650 cells) Li-Ion | (Orange) Li-Po
Ageing | Loses actual charging capacity | Retains charging capacity better than Li-Ion
Energy Density | High Energy Density | Low as compared to Li-Ion
Conversion Rate | The capacity to convert battery into actual power 85-95% | 75-85%
Safety | More Volatile as compared to Li-Poly | More Safety, Less chance of explosion
Cost | Cheaper (200) | Slightly Expensive (+30%)
Weight | Heavier | Light Weight
Charge Duration | Longer Charge | Comparatively Shorter

We are using lithium-ion battery to power the robot. As Lithium-

ion batteries are rechargeable batteries and portable, with a high energy

density.

One cell will provide nearly 6Amperes of current. We are using 3 cells.

### 4.6 BLUETOOTH MODULE (BM-10)

A communication interface is necessary for the robot to convey location information.

PARAMETERS | HC-05 | HC10
Bluetooth version | BLE 2.0/3.0 | BLE4.0
Power consumption | Low | Very Low
cost | Rs 283 /- | Rs 342 /-

We are using Bluetooth module BM-10 (having Bluetooth 4.1 technology).


### 4.7 ROBOT ARM

A robotic arm is a type of mechanical arm. Which can perform near similar to

human arm. Our robotic arm is specially designed by us for pick and place

type task. It is designed by online 3D design software (TinkerCad). And

made using 3D printing technology.

- 3D DESIGN:

We tried various shapes and sizes to obtain maximum grip as well as

high strength. Previously we finalized ‘F’ shaped arms with 4 teeth on each

arm. But it would fail to hold round shaped objects.

So, we provided angles to arm & increased number of teeth so that it

would hold the multiple sides of object and get maximum grip.

Gears are also added so that whole arrangement can be moved using

single actuating element (servo motor).

This 3D structure is designed using an online software ‘TinkerCad’.

- 3D PRINTING:

To fabricate this 3D object, we used 3D printing technology. A special

machine called 3D printer can make this 3D structure. We have to provide

only 3D object file (.stl file) & select the amount of material to be filled.

3D printer is an expensive machine that wasn’t available with us. So, we

took help of a company ‘Infinity Systems’ to fabricate that structure.


- MATERIAL USED:

Three type of materials can be used to print this object:

- HIPS (high impact polystyrene)
- ABS (Acrylonitrile Butadiene Styrene.)
- PLA (polylactic acid).

HIPS is costly material with not so considerable features.

ABS (http://amzn.to/2mdb53v) is widely available (http://amzn.to/2mdb53v) and has been a very popular plastic in the

development of prosumer 3D printing from the start. It melts consistently at

around 225 degrees Celsius, which can easily be achieved with small and home-

safe electronics.

PLA (http://amzn.to/2lXFQJg) is made from corn starch or sugar cane and is biodegradable, so it’s more

environmentally-friendly than ABS. It melts can melt at a lower temperature

between 190 and 210 degrees and doesn’t smell bad when it does.

PLA also has high tensile strength(37Mpa) than ABS (27Mpa).

So, by looking at these advantages we chosen PLA for our application. Because

of high strength Only 25% fill of PLA can satisfy the application need.

### 4.8 CHASSIS DESIGN:

Chassis is internal vehicle frame that provides base and supports an artificial

object in its construction and use, it also provides protection for some internal parts.

Metal plates, fibre, or MDF can be used to make Chassis.

Metal plates are hard to work with. Cutting, drilling, and welding requires special tools &

too much efforts. But MDF can be cut using normal hack-saw blade, and drilling can

also be done easily.

Features | Aluminium Sheet | MDF | Plywood
Cost | High | Low | Moderate
Cutting and drilling | Not easy | Can be cut with hand easily | Not easy
Weight | High | Low | Moderate
Water resistance | No dominant effect of water | It soaks water and swells | It also soaks water slowly
Safety | Hazardous due to sharp edges | Safe | Safe

So, we used MDF material (Medium Density Fibreboard) to make the chassis.

Medium-density fibreboard (MDF) is a wood product made by breaking down hardwood

or softwood residuals into wood fibres, often in a defibrator, combining it with wax and

a resin binder, and forming panels by applying high temperature and pressure. MDF is

generally denser than plywood.

We chose this material because of advantages like light weight and ease of use

MDF is typically made up of 82% Woodfibre, 9%

urea-formaldehyde resin glue, 8% water and

1% paraffin-wax.

### 5. SOFTWARE ASPECTS:

### 5.1 KICAD: -

- This software is used for PCB Designing
- We have designed a controller board for ATMEGA 328P-PU and Motor

driver using L298N using KICAD.

- First, we made a schematic for these boards and then updated PCBs from

schematic by assigning them appropriate footprints.

### 5.2 ARDUINO IDE: -

- Arduino IDE is used for microcontroller programming
- Program consists of programming for Motors, Sensors and Motor driver,

Servo Motor.

### 5.3 PROTEUS: -

- This software is used for simulation purpose
- We have performed simulation of this Smart Wireless controlled Pick-N-

Place Line Following Robot circuitry in order to check whether it is working

or not.

### 5.4 TIKERCAD: -

- TinkerCad is a free, easy-to-use app for 3D design, electronics, and

coding. It's used by teachers, kids, hobbyists, and designers to imagine,

design, and make anything!

- After Designing 3D Model, the STL File is exported and processed with

Slicing Software.

### 6. CIRCUIT DESIGN:

### 6.1 MICROCONTROLLER BOARD:


- 10KOhm resistor on reset pin to avoid accidental resetting of microcontroller
- Switch SW1 for Resetting Circuitry.
- C1, C4, C5 capacitors for filtering supply noise, gives high frequency noise signals low impedance path to ground (0.1 uF is the most common capacitor value). As Xc=1/(2πfC), more is Frequency lesser is Reluctance.
- ISP header for using external programmer using SPI protocol
- 16 MHz crystal for clock
- LED and 1K Resistor to Indicate Power.

### 6.2 MOTOR DRIVER (L298N):


- Max Power 25W.
- Instantaneous Peak Current 3A.
- R6, R7=0Ω(ohm), as we are not using Current Sense.
- Logic Supply of 7V Max.
- 100nF Non-Inductive Capacitor And must be placed as near as possible to GND.
•
6.3 3.3V_REGULATION(AMS1117)
- Cp = 22uF to ensure stable voltage in all operating conditions.

6.4 5V_REGULATION (IC7805):

Provides 5V for Arduino Board and Servo Motor.


- C6 = 0.33uF for filtering input supply Noise.
- C7 = 0.1uF for filtering Output Supply, to ensued stability in all operating Conditions.

### 6.5 MOTOR CALCULATIONS:

Mass of robot = 1.5 KG

Radius of wheel = 5.5 cm = 0.055 m

Torque required = m*g*R | Where -
| m= mass of robot
| G= gravity
| R=radius of wheel

Therefore

Torque = 1.5*9.8*0.055

=0.8085 N.M

### 6.6 SERVO CALCULATIONS:

The servo motor is coupled to one of the arm of robotic arm, & to open the arm fully we

need only 45 degree rotation .So

Duty cycle= 1.5+(angle of rotation in degrees /180)

=1.5+(45 /180)

=1.75 ms

- Weight calculation:

Torque given is 8.5 kg-cm for 4.8v supply

Means it can lift upto 8.5 kg with 1 cm of shaft length

Our arm length is 8.5 cm. So,

Maximum lifting weight = torque/arm length

=8.5/8.5

=1 kg

- Maximum arm opening is 11.3 cm ,so maximum holding length is 11.3cm .

It is supposed to hold objects of 2cm to 10 cm more precisely.

- Arm opening time:

Speed given is 0.2 sec/60deg

Therefore for 45 degree rotation it will take

( 0.2) 45/60= 0.15

It means arm will open or close in 150 msec (for full speed).

### 7. SIMULATION RESULTS:


### - In place of IR Sensor, Switches are used to simulate the

conditions outcomes on Black over Right Line stripes.

### - The Motor speed and directions vary according to the

conditions written in the code.

- The servo motor is operated when the object is detected.

### 8. PCB LAYOUTS:

### 8.1 MICROCONTROLLER BOARD:


SCHEMATIC DIAGRAM


PCB LAYOUT (BOTTON LAYER)


### 8.2 MOTOR DRIVER BOARD:

SCHEMATIC DIAGRAM

PCB LAYOUT (BOTTON LAYER)

### 9. TESTING OF MODULES:

### 9.1 MOTOR DRIVER L298N:

Testing is done to ensure proper functionality of the circuits. Individual circuits &

modules should be tested separately so that there will not be any problems in

further design.


(top)

(BOTTOM)

L298 Board after soldering (2 channel)

We tested the board in 3 steps

- Component test

We checked that, all the components are in place & soldered properly or not.

- Continuity test
- By using DMM we checked the continuity of tracks to ensure the proper

conduction of the circuit.

- Some points that are supposed to be isolated but get connected by mistake

are also found out by continuity test.

- Functionality test
- In this step we check the actual operation of the circuit.
- This includes applying input and checking weather circuit is giving proper

output or not.

- We gave control signals using 5v & GND headers on the board and checked

the output voltage using DMM.

- Output voltage should be positive for clockwise and negative for counter-

clockwise direction.

- We performed this test for both the channels & got proper output.

### 9.2 MICROCONTROLLER BOARD:

We tested the board in 3 steps

- Component test

We checked that, all the components are in place & soldered properly or not.

- Continuity test
- By using DMM we checked the continuity of tracks to ensure the proper

conduction of the circuit.

- Some points that are supposed to be isolated but get connected by mistake

are also found out by continuity test.

- Functionality test
- In this step we check the actual operation of the circuit.
- This includes applying input and checking weather circuit is giving proper

output or not.



### 9.3 HC-09 BLUETOOTH MODULE:

We tested the board in following steps:

- For testing purpose, we interfaced Bluetooth module to the Arduino UNO

board. And wrote a program to display the received data on computer

screen

- We selected alphabets A to G as valid data and all other characters, signs,

spaces & special characters as invalid data.

- We have pin0 and pin1 of UNO board as RX and TX respectively, that we

are using for sending the received data on computer.

- So, we used pins 8 and 9 to interface Bluetooth module. A function called

SoftwareSerial

- Configures the normal GPIO pins as TX and RX for serial

communication.

- Data transmitted through Mobile phone via app Serial Bluetooth terminal
- Arduino has inbuild LED connected on pin 13. We used that LED to

indicate that valid data is received.

-Testing Working of Board
using “avrdude”

- Connection chart
HC-09 | Arduino UNO
State | Nc
RXD | D9
TXD | D8
GND | Gnd

### 9.4 SERVO MOTOR:


As discussed before, Testing is done to ensure proper functionality of the circuits.

Individual circuits & modules should be tested separately so that there will not be any

problems in further design.

For Servo motor we performed only functionality test because it is a ready-made device

& its internal circuits are not easily accessible.

Testing Servo motor requires PWM signal for its operation. Duty cycle of this input

signal decides the angle of rotation of the shaft.

For testing purpose, we interfaced the motor with Arduino UNO (PIN 3).

-Snap of Mobile App and Serial Terminal

And wrote a program to rotate the motor in both directions.

Connections: -

Servo pins | Arduino Uno pins
PWM | PIN 3
VCC | +5V
GND | GND

Program
#include <Servo.h> | // Include Servo library

int servoPin = 3; | // Declare the Servo pin
Servo Servo1; | // Create a servo object
void setup()
{
Servo1.attach(servoPin); // define pin 3 for servo1 }
void loop()
{
Servo1.write(0); // go to 0 degrees delay(1000);
Servo1.write(90); // go to 90 degrees delay(1000);
Servo1.write(180); // go to 180 degrees delay(1000);

}


### 9.5 INFRARED MODULE:

- We used IR sensor array for line sensing. It is array of five IR sensors with 5 digital outputs.
- It gives 0 & 1 signals for black and white colour respectively.
- We performed functionality test for this module.
- By interfacing the IR array to Arduino Uno board, we transmitted the signal on serial terminal of pc.
- And checked the outputs by moving the sensor array on black and white backgrounds.

Connections
IR module | Arduino Uno
Sensor1 | 8
Sensor2 | 9
Sensor3 | 10
Sensor4 | 11
Sensor5 | 12
VCC | +5V
GND | GND

Test program
const int mod1 = 8;
const int mod2 = 9;
const int mod3 = 10;
const int mod4 = 11;
const int mod5 = 12;

unsigned long int val = 0b00000000; //variable to store Sensor data

void serialprint()
{
Serial.println(PINB, BIN); Serial.println("_______________________"); }
void setup()
{
Serial.begin(9600); | //set baudrate 9600
DDRB = 0x00; | // make port B as output
delay(1000);
}

void loop()
{
serialprint(); | //send sensor values on serial terminal
uint8_t val = PINB; | //copy the sensor values in a variable
}


-IR Sensor testing with Black line on White Background.


### 10. CABINET DESIGN AND ASSEMBLY:


11.BILL OF MATERIALS:

Sr. No | Component Name | Value | Quantity | Amount
1 | PCB Manufacturing (Acetone, Copper clad, FeCl3, Safety Gloves,) | | 2 | 200₹
2 | ATmega328-PU | 28pin DIP | 1 | 125₹
3 | AMS1117-3.3 | SOT-23 | 1 | 5₹
4 | L298HN | TO-220(15) | 1 | 110₹
5 | L7805 | TO-220(3) | 1 | 10₹
6 | Crystal HC18-U | 16MHz | 1 | 4₹
7 | Resistor THT | 10K, 1K | 4 | 1₹
8 | Capacitor Disc THT | 1uF | 4 | 2₹
9 | LED | 3.5mm | 2 | 6₹
10 | JST Connection Header | 3pin male | 3 | 16₹
11 | Motor | (wrf-530Tc-12560) | 1 | 300₹
12 | Diode 1N4001 | THT | 9 | 9₹
13 | Button Switch | 4pin | 1 | 10₹/piece
14 | Capacitor Disc THT | 100nF, 470uF,.33uF | 1 | 9₹
15 | Connection Header Male | 2.54pitch | 1 | 6₹
16 | Connection Header Female | 2.54pitch | 1 | 6₹
17 | Wheels | 6cm | 2 | 120₹
18 | Servo Motor | MG995 | 1 | 350₹
20 | Chassis (MDF, Motor hinges, Screws, nuts washers,) | | | 200₹

1489₹

Approximate Budget is 1500₹.

### 12. REFERENCES:

-ARDUINO DESIGN:https://www.allaboutcircuits.com/technic-alarticles/understanding-arduino-uno-hardware-design/ (https://www.allaboutcircuits.com/technic-alarticles/understanding-arduino-uno-hardware-design/)

-SG90: http://www.ee.ic.ac.uk/pcheung/teaching/DE1_EE/stores/sg90_datasheet.pdf

-MG995: https://www.towerpro.com.tw/product/mg995/

-BLUETOOTH MODULE: https://howtomechatronics.com/tutorials/arduino/arduino-and-hc-05-bluetooth-module-tutorial/ (https://howtomechatronics.com/tutorials/arduino/arduino-and-hc-05-bluetooth-module-tutorial/)

-MDF: https://en.wikipedia.org/wiki/Medium-density_fibreboard

-3D Design: https://www.tinkercad.com/things/dJmnHaHhOIF-grand-snaget-amur/edit

-Materials: https://www.3dhubs.com/knowledge-base/pla-vs-abs-whats-difference

-MDF Plywood : https://www.livspace.com/magazine/mdf-vs-plywood-comparison/


### 13. PROJECT PHOTO:

- Hardware:

-3d model of Mosfet Driver as Designed on KiCad

-3d model of Microcontroller Board as Designed on KiCad


-Drilling of Boards

-Etching of Boards

-Soldering of Boards


-MOSFET Driver after Soldering (Top side on left)

-Microcontroller Board after Soldering (Top side on left)

### 14. CONCLUSION:

The design and development of pick and place robot has been carried out. A

prototype was confirmed functional working of robot system. This system would make it

easier for human beings to pick and place the risk of handling suspicious objects, which

could be hazardous in its present environment and workplace. Complex and complicated

duties can be achieved faster and more accurately with this design.

A robotic arm is implemented using Atmega328P-PU in pick and place objects

more safely without incurring much damage. The robotic arm used here contains a soft

catching gripper, which safely handles the object. In the modern era, time and man power

are major constraints for the completion of a task.

By the use of product, the industrial activities and hazardous operations can be done

easily and safely in a short span of time. The use of soft catching gripper and low power

wireless communication technique like BLE (4.0) makes our system more effective when

compared to other systems. The developed system is capable of lifting only small

weights; by introducing high torque motor large weights can be picked. A wireless

camera can also be implemented to track the movement of the vehicle and thus it can be

used for defense purposes. The range is also a limitation here but it can be enhanced.

15.DATASHEETS:

-pto

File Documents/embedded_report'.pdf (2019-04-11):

A

### Report

On

# “Embedded System Design Using MSP430.”

### Submitted By:

### Arpit Shrivastava (312059)

### Durgesh Vitore (312070)

### Tejas Shinde (312058)


DEPARTMENT OF ELECTRONICS AND TELECOMMUNICATION ENGINEERING, VISHWAKARMA INSTITUTE OF INFORMATION TECHNOLOGY, PUNE– 411048
YEAR 2018-2019

## Introduction to MSP430:-

The MSP microcontrollers (MCUs) from Texas Instruments (TI) are 16-bit and 32-bit RISC-based, mixed signal processors designed for ultra-low power applications. The MSP430 family of microcontrollers consists of several devices featuring different sets of peripherals targeted for various applications. The MSP430 device features a powerful 16-bit RISC CPU, 16-bit registers, and constant generators that contribute to maximum code efficiency. The architecture, which includes five low-power modes, is optimized to achieve extended battery life in portable measurement applications. The digitally controlled oscillator (DCO) allows wake-up from low-power modes to active mode in less than 1 microsecond.
The MSP430 instruction set consists of 27 core instructions that make it easy to program in assembler or in C, and provide exceptional flexibility and functionality. MSP low-power + performance microcontrollers from TI provide designers with enhanced performance and more peripherals on chip while using less power. MSP ultra-low-power microcontrollers are ideal for applications where the majority of the microcontroller life is spent in standby. Typical applications of these processors include low-cost sensor systems that capture analog signals, convert them to digital values, and then process the data for display or for transmission to a host system.
The architecture of the MSP430 family is based on a memory-to-memory architecture, a common address space for all functional blocks, and a reduced instruction set applicable for all functional blocks. The MSP430G2553 CPU has a 16-bit RISC architecture integrated with 16 registers that provide reduced instruction execution time. All operations, other than program-flow instructions, are performed as register operations. Memory of the MSP430G2553 is divided to program memory (ROM) and data memory (RAM). The program memory is accessed by the 16-bit Memory Data bus. The data memory is accessed by the Memory Address Bus (MAB) and the Memory Data Bus (MDB).
Peripheral modules such as Digital I/O, Analog-to-Digital Converter (ADC), Timers, Universal Asynchronous Receiver Transmitter (UART), Universal Serial Communications Interface (USCI), Comparator A+, etc., are connected to the CPU via MAB, MDB and interrupt service and request lines. The operations of the various peripherals are controlled by the contents of the Special Function Registers (SFRs). The clock system is supported by the basic clock module that includes support for a 32768-Hz watch crystal oscillator, an internal very-low-power, low-frequency oscillator and an internal Digitally Controlled Oscillator (DCO). The brownout circuit is implemented to provide the proper internal reset signal to the device during power on and power off.

The brownout circuit is implemented to provide the proper internal reset signal to the device during power on and power off.
The Watchdog Timer (WDT+) module restarts the system on occurrence of a software problem or if a selected time interval expires. The WDT can also be used to generate timely interrupts for an application.

So some of the main features of MSP430 includes:
Low supply voltage range: 1.8 V to 3.6 V
Low-power consumption:
220 A / MHz active mode.
0.7 A real-time clock mode.
A RAM retention.
16-bit RISC Architecture:
Basic clock module configurations:
Internal frequencies up to 16 MHz with four calibrated frequency Serial communication modules:
USART
USI
Memory:
Up to 56 KB Flash
Up to 4 KB SRAM

MSP430 Pinout Diagram:


## Code Composer Studio (Software):-

Code Composer Studio (CCS) is the integrated development environment for the whole span of TI Microcontrollers, DSPs and application processors. Code Composer Studio includes a suite of tools used to develop and debug embedded applications. For all device families, CCS includes compilers, source code editor, project build environment, debugger, profiler, simulators and many other features. Code Composer Studio v6 is the latest version of the IDE used currently and is based on Eclipse 4.3, whereas the earlier version CCSv5 was based on the Eclipse 3.x stream.
The CCS App center, introduced in CCSv6, lists all the relevant packages for the chosen devices during the installation. The Getting Started View, which is open by default when CCS is first launched, provides fast access to many of the common tasks the users would prefer to experiment when starting to use a new environment, such as creating a new project, browsing examples and visiting the App Center. There are also links to the support forums, YouTube videos, training material and the wiki. There is also a video that is prominently displayed in the center of the screen that walks users through the steps to use the CCS environment
The CCS supports all the phases of the development cycle: design, code and build, debug. The CCS includes all the development tools - compilers, assembler, linker, debugger, BIOS and one target - the Simulator

CSS Functional Overview:-

- The C compiler converts C source code into assembly language source code. The assembler translates assembly language source files into machine language object files.
- The standard run-time libraries contain ANSI standard run-time-support functions, compiler-utility functions, floating-point arithmetic functions and I/O functions that are supported by the C compiler.
- The linker combines object files, library files and system or BIOS configuration files into a single executable object module. The .out file is the executable program for the target device. etc. The .gel files initialize the debugger with address of memory, peripherals and other hardware setup details.

## Getting Started With Programming:-

Project Creation and Build –

1. Click File New CCS Project
2. Type in your “Project name” and make the selections shown below (your dialog may

look slightly different than this one).

3. If you are using the MSP430G2553, make the appropriate choices for that part. Make

sure to click Empty Project (with main.c) and then click Finish.

4. If you are writing an Assembly Code, select Empty Assembly-only Project.
5. Code Composer will add the named project to your workspace and display it in the

Project Explorer pane. Based on your template selection, it will also add a file called

main.c/ main.asm and open it for editing.

6. Change the include header file statement from #include to #include .
7. Type in your program code in the main.c / main.asm file and save it.
8. CCS can automatically save modified source files, build the program, open the debug

perspective view, connect and download it to the target (flash device), and then run the

program to the beginning of the main function. To do this, click on the "Debug" button.

9. When the Ultra-Low-Power Advisor (ULP Advisor) appears, click the Proceed button.
10. When the download completes, CCS is in the Debug perspective. Notice the Debug

tab in the upper right-hand corner indicating that we are now in the "CCS Debug" view.

11. Click and drag the perspective tabs to the left until you can see all of both tabs. You

can observe that the program has run through the C-environment initialization routine in

the runtime support library and stopped at main() in main.c.

## Other Software Development Environment’s:-

Texas Instruments provides various hardware experimenter boards that support large (approximately two centimeters square) and small (approximately one millimeter square) MSP430 chips. TI also provides software development tools, both directly, and in conjunction with partners (see the full list of compilers, assemblers, and IDEs). One such toolchain is the IAR C/C++ compiler and Integrated development environment, or IDE.
TI also combines a version of its own compiler and tools with its Eclipse-based Code Composer Studio IDE ("CCS"). It sells full-featured versions, and offers a free version for download which has a code size limit of 16 KB. CCS supports in-circuit emulators, and includes a simulator and other tools; it can also work with other processors sold by TI.
For those who are more comfortable with the Arduino, there is also another software Energia, an open source electronics prototyping platform with the goal to bring the Wiring and Arduino framework to the Texas Instruments MSP430 based LaunchPad where Arduino code can be exported for programming MSP430 chips.
The open source community produces a freely available software development toolset based on the GNU toolset.
TI consulted with RedHat to provide official support for the MSP430 architecture to the GNU Compiler Collection C/C++ compiler. This msp430-elf-gcc compiler is supported by TI's Code Composer Studio version 6.0 and higher.
There is a very early llvm-msp430 project, which may eventually provide better support for MSP430 in LLVM.
Other commercial development tool sets, which include editor, compiler, linker, assembler, debugger and in some cases code wizards, are available. VisSim, a block diagram language for model based development, generates efficient fixed point C-Code directly from the diagram.[6] VisSim generated code for a closed loop
ADC+PWM based PID control on the F2013 compiles to less than 1 KB flash and 100 bytes RAM.[7] VisSim has on-chip peripheral blocks for thentire MSP430 family I²C, ADC, SD16, PWM.

## PWM Motor Control using MSP430:


Pulse Width Modulation (PWM) is a method of digitally encoding analog signal levels. High-resolution digital counters are used to generate a square wave of a given frequency, and the duty cycle of the square wave is modulated to encode the analog signal. The duty cycle determines the time during which the signal pulse is HIGH.

As from above figure it is clear that average Analog voltage increases with increase in Duty Cycle. More is the voltage across Motor more will be the speed.

Interfacing Diagram:-

Hardware and Software requirements:-
MSP430G2 LaunchPad
Code Composer Studio.

Flowchart:-


C Program Code:

#include <msp430.h>

int a[5] = {0,32,64,128,255};
int i = 0;
void main(void){
WDTCTL = WDTPW|WDTHOLD; | // Stop WDT
//IE1 |= WDTIE; | // enable Watchdog timer interrupts
P1DIR |= BIT6; | // Motor for output
P1SEL |= BIT6; | // Motor Pulse width modulation

TA0CCR0 = 512; | // PWM period
TA0CCR1 = a[0]; | // PWM duty cycle
TA0CCTL1 = OUTMOD_7; | // TA0CCR1 reset/set-high voltage
// below count, low voltage when past TA0CTL = TASSEL_2 + MC_1 + TAIE +ID_3;
// Timer A control set to SMCLK, 1MHz // and count up mode MC_1
_bis_SR_register(LPM0_bits + GIE); // Enter Low power mode 0 while (1);
}
#pragma vector= TIMER0_A1_VECTOR // Watchdog Timer ISR __interrupt void timer(void) {

TA0CTL &= ~TAIFG;
TA0CCR1 = a[++i];
if (i>4)
{
i=0;
}
}


Calculations for Duty Cycle:

## Conclusion:

The MSP430 Value Line controllers are cheaper than the higher-end ATMega controllers used in the Arduino platform. We don’t need an external crystal, because the MSP430 controllers can run at the full 16 Mhz from their internal clock source. With the MSP430 Launchpad, TI offers a development board which includes:
A programmer for the MSP430 controllers.
Comes with two microcontrollers.
The USB connection also allows you to talk to the microcontroller via a serial connection at 9600 baud,

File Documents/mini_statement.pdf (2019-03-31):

A

Mini Project

Synopsis on

# “Smart WiFi Controlled Pick-N-Place Line Following Robot”

Submitted By:

Arpit Shrivastava (312059) Durgesh Vitore (312070)
Tejas Shinde (312058)


DEPARTMENT OF
ELECTRONICS AND TELECOMMUNICATION ENGINEERING, VISHWAKARMA INSTITUTE OF INFORMATION TECHNOLOGY, PUNE– 411048

YEAR 2018-2019

## Title: Smart WiFi Controlled Pick-N-Place Line Following Robot

Brief Description of Project:
- Robot will be used to Pick-N-Place object from different locations.
- There can be N number of destination locations.
- The locations for picking or placing objects are given over WiFi to the Robot.
- Robot follows the path using Line (White over Black line) as the guideline and reach to the destined location.
- The arm over the bot picks the object once it is detected in front.
- After picking up it makes a 180* turn and then return back to the starting position/position according to the command from user.
- In future, camera module will be implemented along with Raspberry Pi and the user will also get to choose what object the bot have to pick.
- Use: This Robot can have application in autonomous garbage collection, items or goods management in warehouses of delivery companies, or to do any autonomous work on any specified location.

Block Diagram/Circuit Diagram:

MicroController; ATMEGA328P-PU; WiFi Module; Servo Motor; Motor Driver; Motors; IR Detector; Mobile App; Arm; IR Line Sensor Array

Component List:
Robot chassis | 400rs
Motors | 500rs
Tyres | 50rs
Battery | 400rs
Switch | 10rs
Microcontroller (ATMEGA328p-Pu) | 110rs
Wifi (Esp8266-12E) | 150rs
Motor Driver(L293D) | 200rs
Servo Motors [2] | 300rs
Arm mechanism | 150rs
IR Line Sensor | 150rs
2420rs

Approximate Budget: approximately 2500rs.

Reference:-
- Espressif.com
- Arduino.com

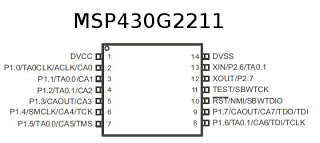
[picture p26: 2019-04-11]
Documents/G2211_pinout.jpg

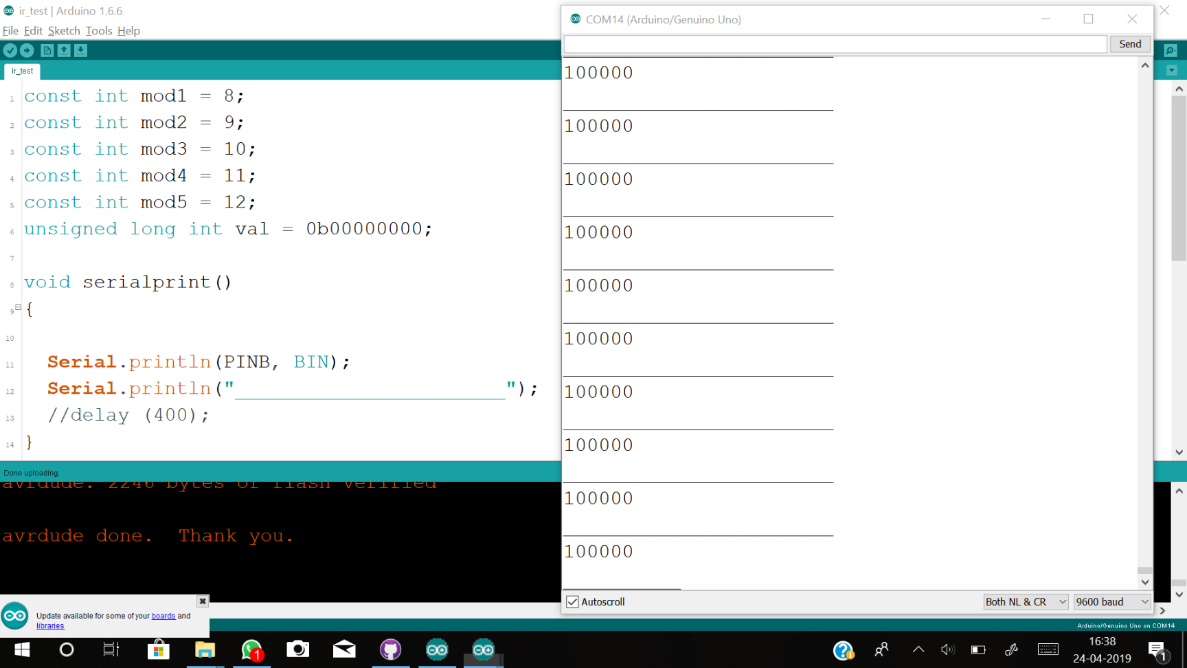
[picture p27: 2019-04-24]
Sketch.png

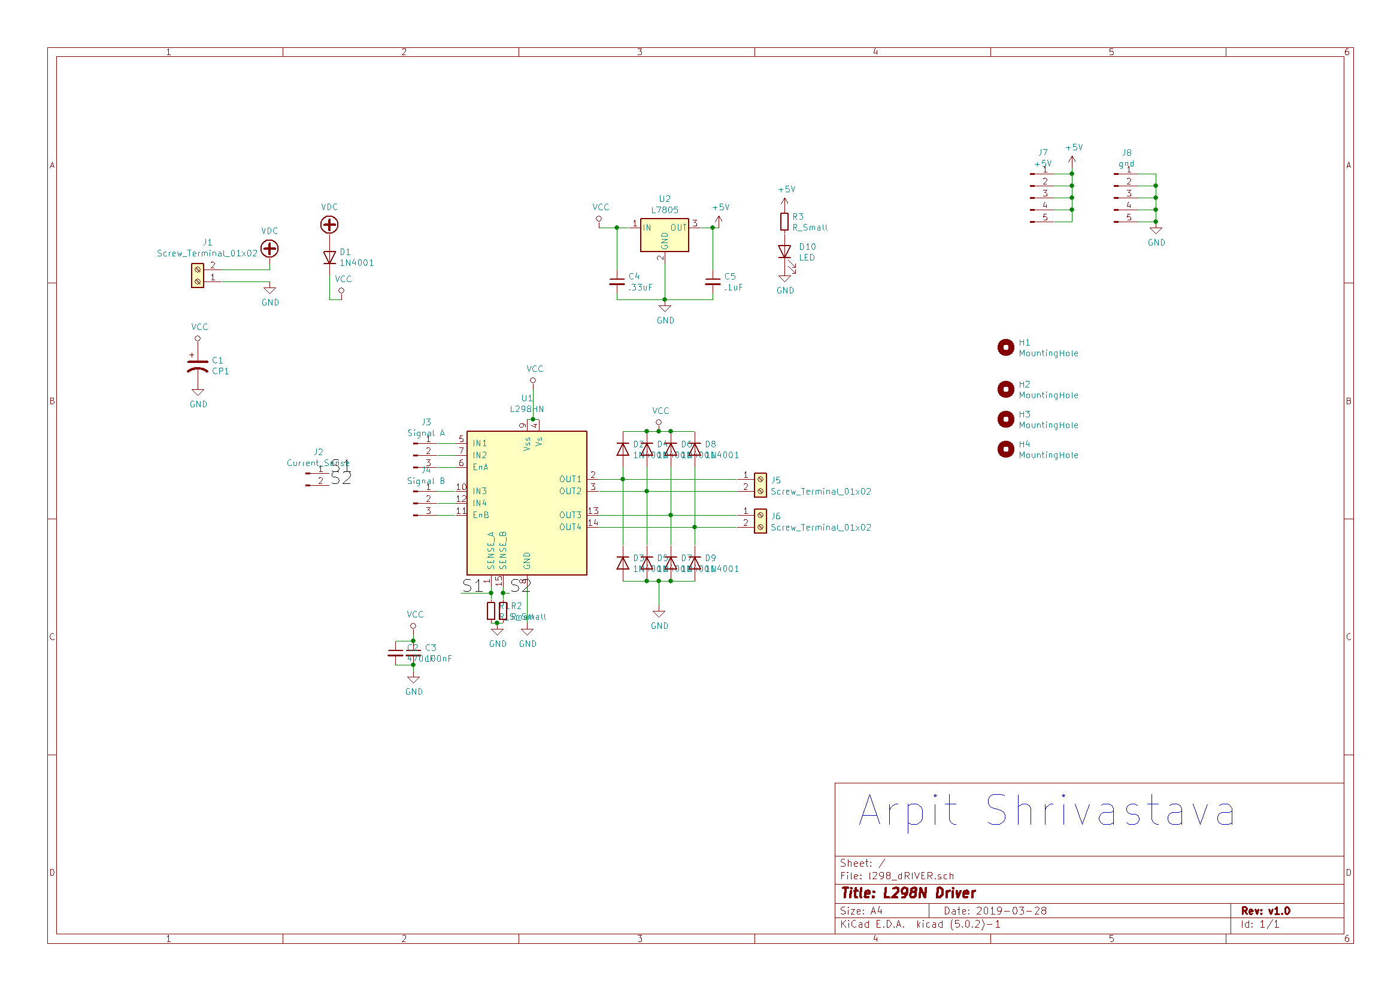
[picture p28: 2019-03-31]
Documents/motor_driver.png

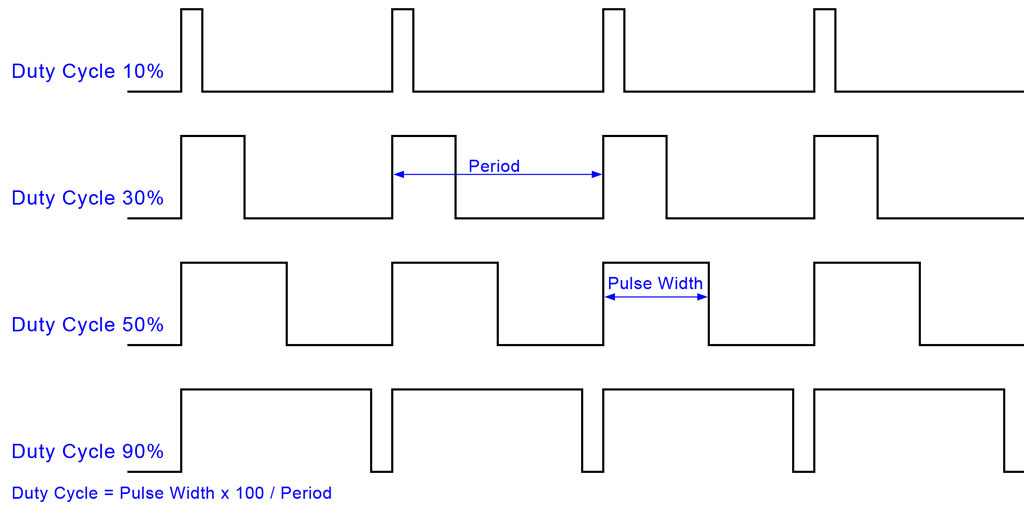
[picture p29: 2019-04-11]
Documents/atmega168a_pwm_02_lrg.jpg

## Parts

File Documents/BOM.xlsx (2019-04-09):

SW1 | SW_Push | Button_Switch_THT:SW_PUSH_6mm
R3 | 10K | Resistor_THT:R_Axial_DIN0207_L6.3mm_D2.5mm_P7.62mm_Horizontal
Y1 | Crystal | Crystal:Crystal_HC18-U_Vertical
C4 | .1uF | Capacitor_THT:C_Disc_D3.0mm_W1.6mm_P2.50mm
U2 | ATmega328-PU | Package_DIP:DIP-28_W7.62mm_Socket_LongPads
C5 | .1uF | Capacitor_THT:C_Disc_D3.0mm_W1.6mm_P2.50mm
C3 | CP | Capacitor_THT:CP_Radial_D10.0mm_P2.50mm_P5.00mm
J1 | Conn_01x06_Male | Connector_PinSocket_2.54mm:PinSocket_1x06_P2.54mm_Vertical
C1 | .1uF | Capacitor_THT:C_Disc_D3.0mm_W1.6mm_P2.50mm
J5 | . | Connector_IDC:IDC-Header_2x05_P2.54mm_Vertical
J3 | JST_XH_3P | Connector_JST:JST_XH_B03B-XH-A_1x03_P2.50mm_Vertical
J4 | JST_XH_3P | Connector_JST:JST_XH_B03B-XH-A_1x03_P2.50mm_Vertical
J2 | ESP01 Module | Connector_PinHeader_2.54mm:PinHeader_2x04_P2.54mm_Vertical
U1 | AMS1117-3.3 | Package_TO_SOT_SMD:SOT-223-3_TabPin2
C2 | CP | Capacitor_THT:CP_Radial_D10.0mm_P2.50mm_P5.00mm
R1 | 1K | Resistor_THT:R_Axial_DIN0207_L6.3mm_D2.5mm_P7.62mm_Horizontal
R2 | 1K | Resistor_THT:R_Axial_DIN0207_L6.3mm_D2.5mm_P7.62mm_Horizontal
J7 | AVR-ISP-6 | Connector_PinHeader_2.54mm:PinHeader_2x03_P2.54mm_Vertical
J6 | Serial_Conn | Connector_PinHeader_2.54mm:PinHeader_1x03_P2.54mm_Vertical
J8 | Screw_Terminal_01x02 | TerminalBlock:TerminalBlock_Altech_AK300-2_P5.00mm
R4 | 1K | Resistor_THT:R_Axial_DIN0207_L6.3mm_D2.5mm_P7.62mm_Horizontal
D1 | LED | LED_THT:LED_D3.0mm
L298N
U1 | L298HN | Package_TO_SOT_THT:TO-220-15_P2.54x2.54mm_StaggerOdd_Lead4.58mm_Vertical
R1 | R_Small | Resistor_THT:R_Axial_DIN0207_L6.3mm_D2.5mm_P7.62mm_Horizontal
R2 | R_Small | Resistor_THT:R_Axial_DIN0207_L6.3mm_D2.5mm_P7.62mm_Horizontal
J5 | Screw_Terminal_01x02 | TerminalBlock:TerminalBlock_Altech_AK300-2_P5.00mm
J6 | Screw_Terminal_01x02 | TerminalBlock:TerminalBlock_Altech_AK300-2_P5.00mm
D2 | 1N4001 | Diode_THT:D_DO-41_SOD81_P7.62mm_Horizontal
D4 | 1N4001 | Diode_THT:D_DO-41_SOD81_P7.62mm_Horizontal
D6 | 1N4001 | Diode_THT:D_DO-41_SOD81_P7.62mm_Horizontal
D8 | 1N4001 | Diode_THT:D_DO-41_SOD81_P7.62mm_Horizontal
D3 | 1N4001 | Diode_THT:D_DO-41_SOD81_P7.62mm_Horizontal
D5 | 1N4001 | Diode_THT:D_DO-41_SOD81_P7.62mm_Horizontal
D7 | 1N4001 | Diode_THT:D_DO-41_SOD81_P7.62mm_Horizontal
D9 | 1N4001 | Diode_THT:D_DO-41_SOD81_P7.62mm_Horizontal
J3 | Signal A | Connector_PinHeader_2.54mm:PinHeader_1x03_P2.54mm_Vertical
J4 | Signal B | Connector_PinHeader_2.54mm:PinHeader_1x03_P2.54mm_Vertical
J1 | Screw_Terminal_01x02 | TerminalBlock:TerminalBlock_Altech_AK300-2_P5.00mm
C1 | CP1 | Capacitor_THT:CP_Radial_D10.0mm_P2.50mm_P5.00mm
C3 | 100nF | Capacitor_THT:C_Disc_D3.4mm_W2.1mm_P2.50mm
C2 | 470uF | Capacitor_THT:C_Disc_D3.4mm_W2.1mm_P2.50mm
J2 | Current_Sense | Connector_PinHeader_2.54mm:PinHeader_1x02_P2.54mm_Vertical
U2 | L7805 | Package_TO_SOT_THT:TO-220-3_Vertical
J7 | +5V | Connector_PinHeader_2.54mm:PinHeader_1x05_P2.54mm_Vertical
J8 | gnd | Connector_PinHeader_2.54mm:PinHeader_1x05_P2.54mm_Vertical
D1 | 1N4001 | Diode_THT:D_DO-41_SOD81_P7.62mm_Horizontal
C4 | .33uF | Capacitor_THT:C_Disc_D3.4mm_W2.1mm_P2.50mm
C5 | .1uF | Capacitor_THT:C_Disc_D3.4mm_W2.1mm_P2.50mm
R3 | R_Small | Resistor_THT:R_Axial_DIN0207_L6.3mm_D2.5mm_P7.62mm_Horizontal
D10 | LED | LED_THT:LED_D3.0mm

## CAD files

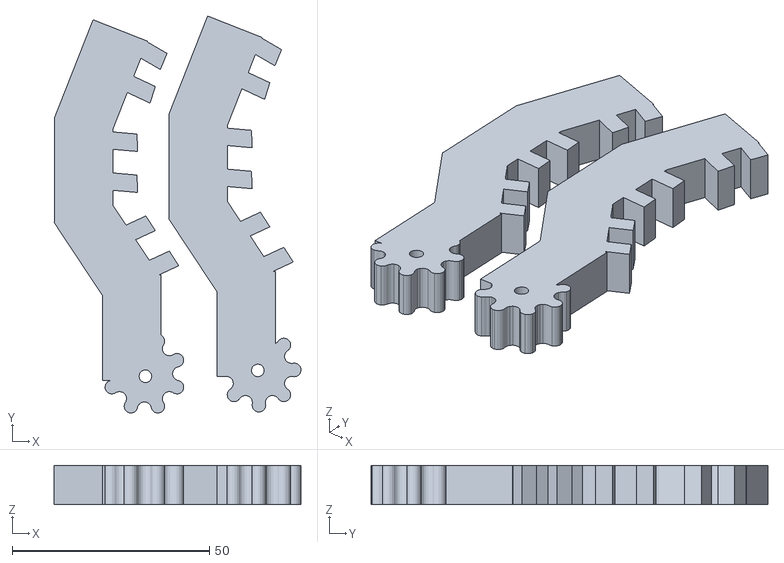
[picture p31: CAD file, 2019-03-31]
Documents/Amazing Lahdi-Luulia.stl
62.5 x 100.5 x 10.0

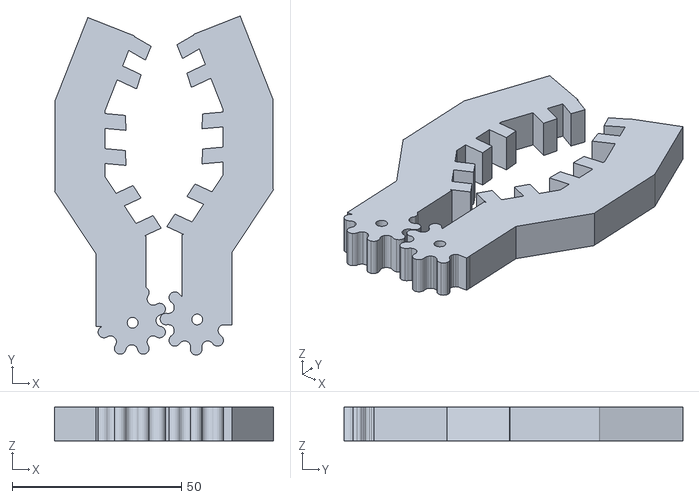
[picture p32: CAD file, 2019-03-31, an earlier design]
Documents/Amazing Lahdi-Luulia (1).stl
64.8 x 100.3 x 10.0

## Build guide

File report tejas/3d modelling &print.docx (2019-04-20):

3D modelling and print of robotic arm

Robotic arm:-

A robotic arm is a type of mechanical arm. Which can perform near similar to human arm. Our robotic arm is specially designed by us for pick and place type task.

It is designed by online 3D design software

(tinkercad). And made using 3D printing technology.

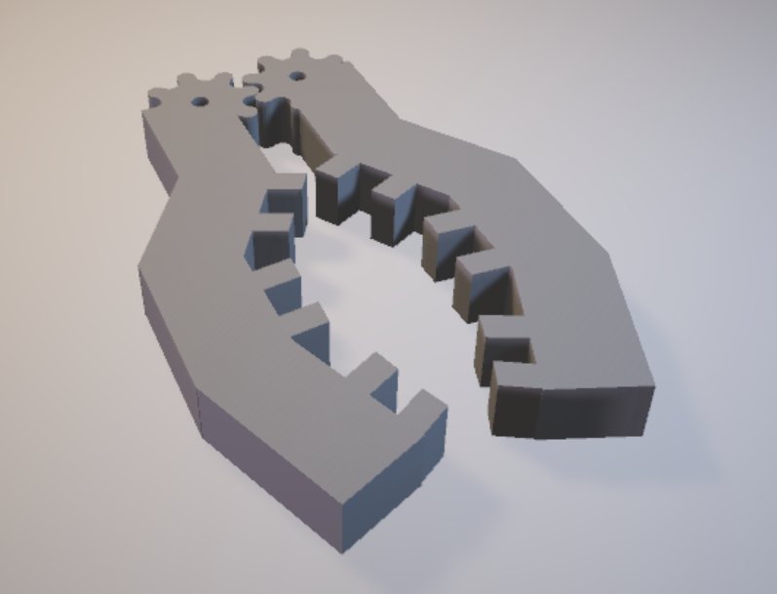
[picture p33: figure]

Provided with multiple teeth structure for maximum grip. And angular structure for holding flat as well as round objects.

Design

We tried various shapes and sizes to obtain maximum grip as well as high strength. Previously we finalized ‘F’ shaped arms with 4 teeth on each arm. But it would fail to hold round shaped objects.

So we provided angles to arm & increased number of teeth so that it would hold the multiple sides of object and get maximum grip.

Gears are also added so that whole arrangement can be moved using single actuating element(servo motor).

This 3D structure is designed using an online software ‘tinkercad’.

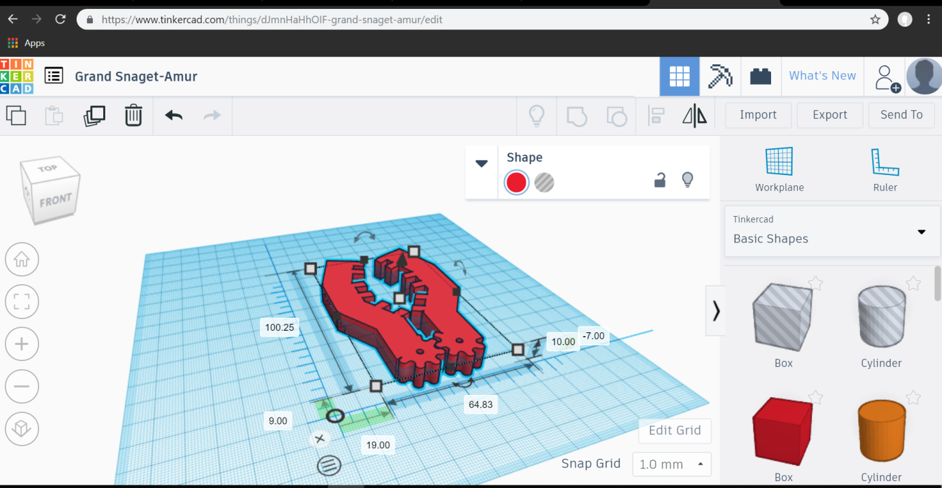
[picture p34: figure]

Printing

To fabricate this 3D object, we used 3D printing technology. A special machine called 3D printer can make this 3D structure. We have to provide only 3D object file(.stl file) & select the amount of material to be filled.

3D printer is an expensive machine that wasn’t available with us. So we took help of a company ‘Infinity Systems’ to fabricate that structure.

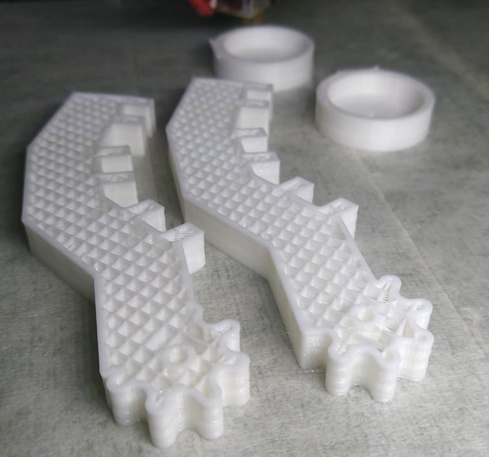
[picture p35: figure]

Material used:

Three type of materials can be used to print this object HIPS(high impact polysterene),ABS(Acrylonitrile Butadiene Styrene.) & PLA(polylactic acid).

Out of which ABS (http://amzn.to/2mdb53v) is widely available (http://amzn.to/2mdb53v) and has been a very popular plastic in the development of prosumer 3D printing from the start. It melts consistently at around 225 degrees Celsius, which can easily be achieved with small and home-safe electronics.

PLA (http://amzn.to/2lXFQJg) is made from corn starch or sugar cane and is biodegradable, so it’s more environmentally-friendly than ABS. It melts can melt at a lower temperature between 190 and 210 degrees and doesn’t smell bad when it does.

PLA also has high tensile strength(37Mpa)than ABS(27Mpa).

So by looking at these advantages we chosen PLA for our application. Because of high strength Only 25% fill of PLA can satisfy the application need.

Referances

3D Design https://www.tinkercad.com/things/dJmnHaHhOIF-grand-snaget-amur/edit

Materials https://www.3dhubs.com/knowledge-base/pla-vs-abs-whats-difference

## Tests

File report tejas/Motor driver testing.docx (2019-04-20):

Motor driver L298N

Testing

Testing is done to ensure proper functionality of the circuits. Indivisual circuits & modules should be tested saperately so that there will not be any problems in further design.

L298 Board after soldering( 2 channel)

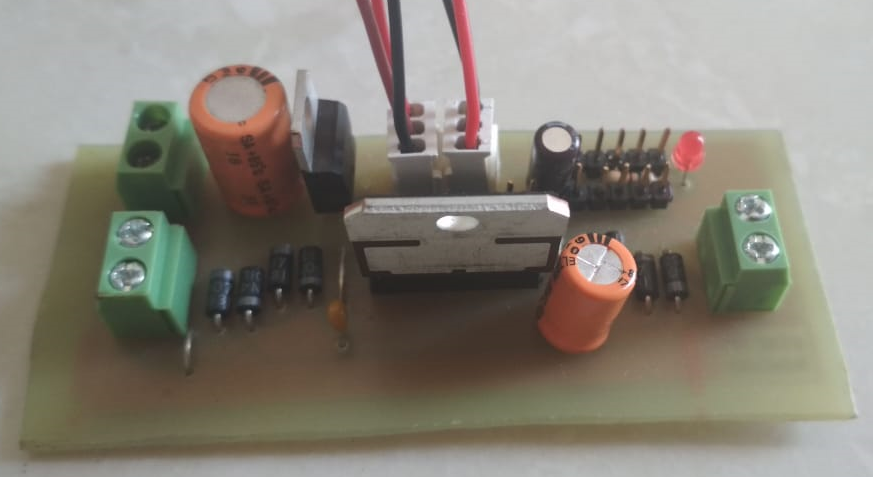
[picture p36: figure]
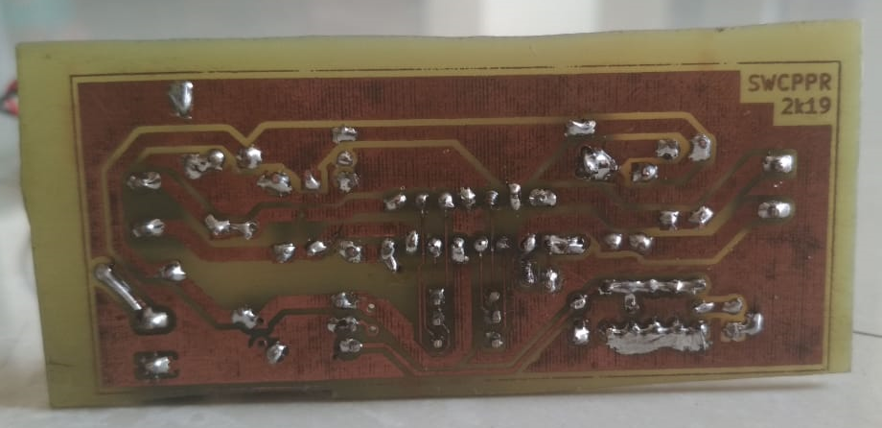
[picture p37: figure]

We tested the board in 3 steps

- Component test

We checked that ,all the components are in place & soldered properly or not.

- Continuity test
- By using DMM we checked the continuity of tracks to ensure the proper conduction of the circuit.
- Some points that are supposed to be isolated but get connected by mistake are also found out by continuity test.
- Functionality test
- In this step we check the actual operation of the circuit.
- This includes applying input and checking weather circuit is giving proper output or not.
- We gave conrol signals using 5v & GND headers on the board and checked the output voltage using DMM.
- Output voltage should be positive for clockwise and negative for counter-clockwise direction.
- We performed this test for both the channels & got proper output.

////////??????testing images

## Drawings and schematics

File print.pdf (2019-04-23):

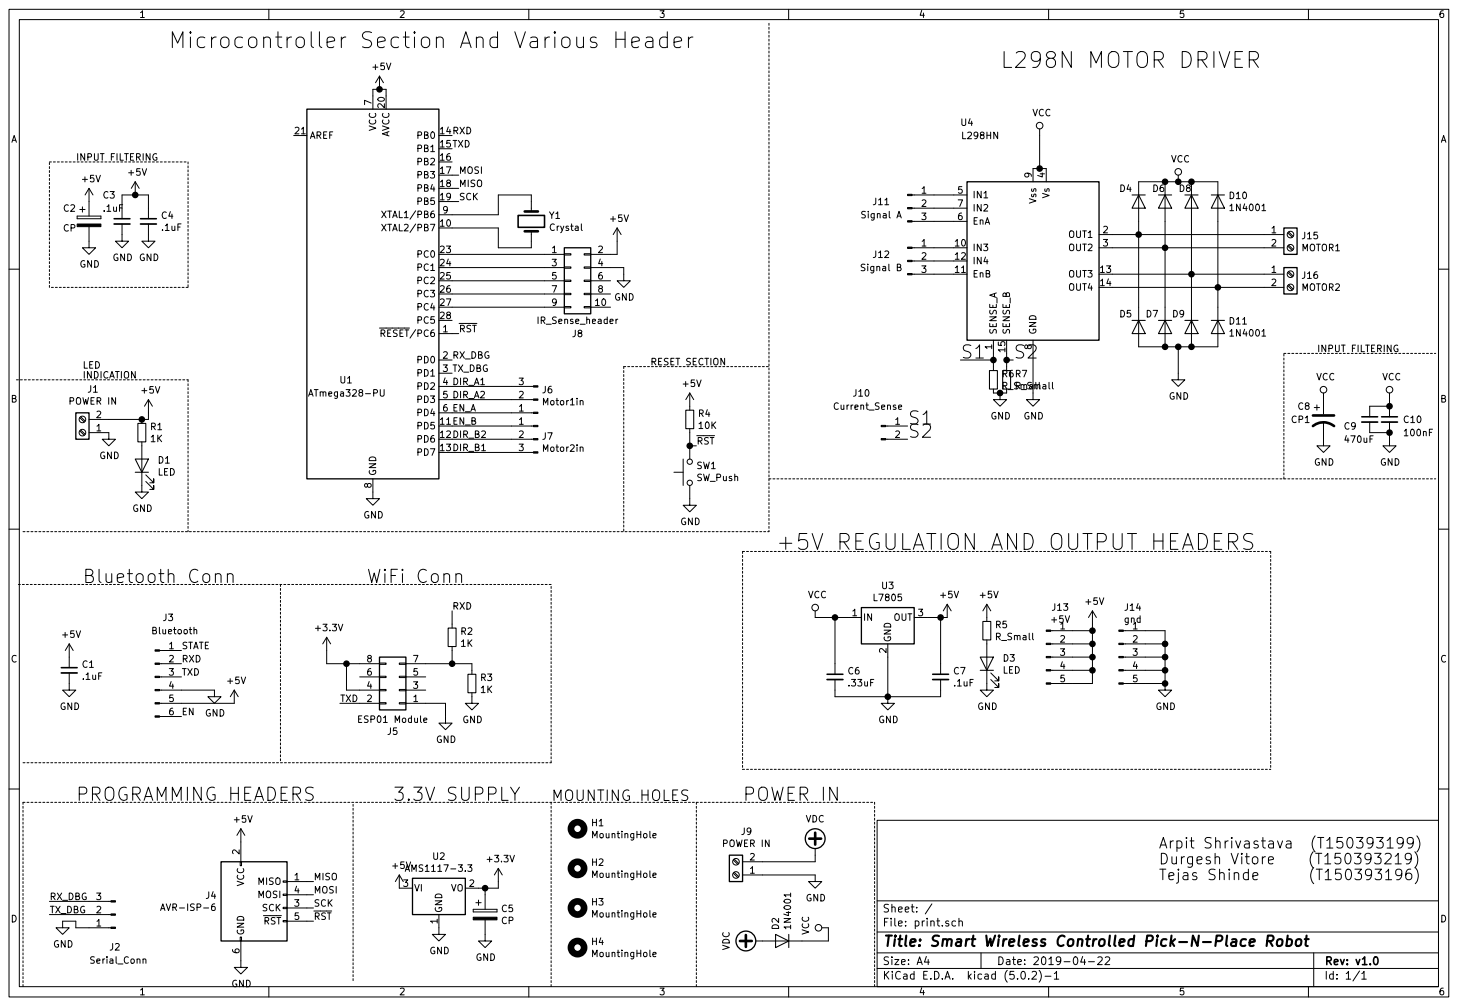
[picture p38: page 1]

J7Motor2in RXD
TXD
SCK MISO MOSI MISO MOSI SCK RST

9 | 10

INPUT FILTERING +5V REGULATION AND OUTPUT HEADERS

2 SCK 3 MOSI 4 RST 5 GND

File: print.sch Sheet: /
Id: 1/1 Title: Smart Wireless Controlled Pick-N-Place Robot

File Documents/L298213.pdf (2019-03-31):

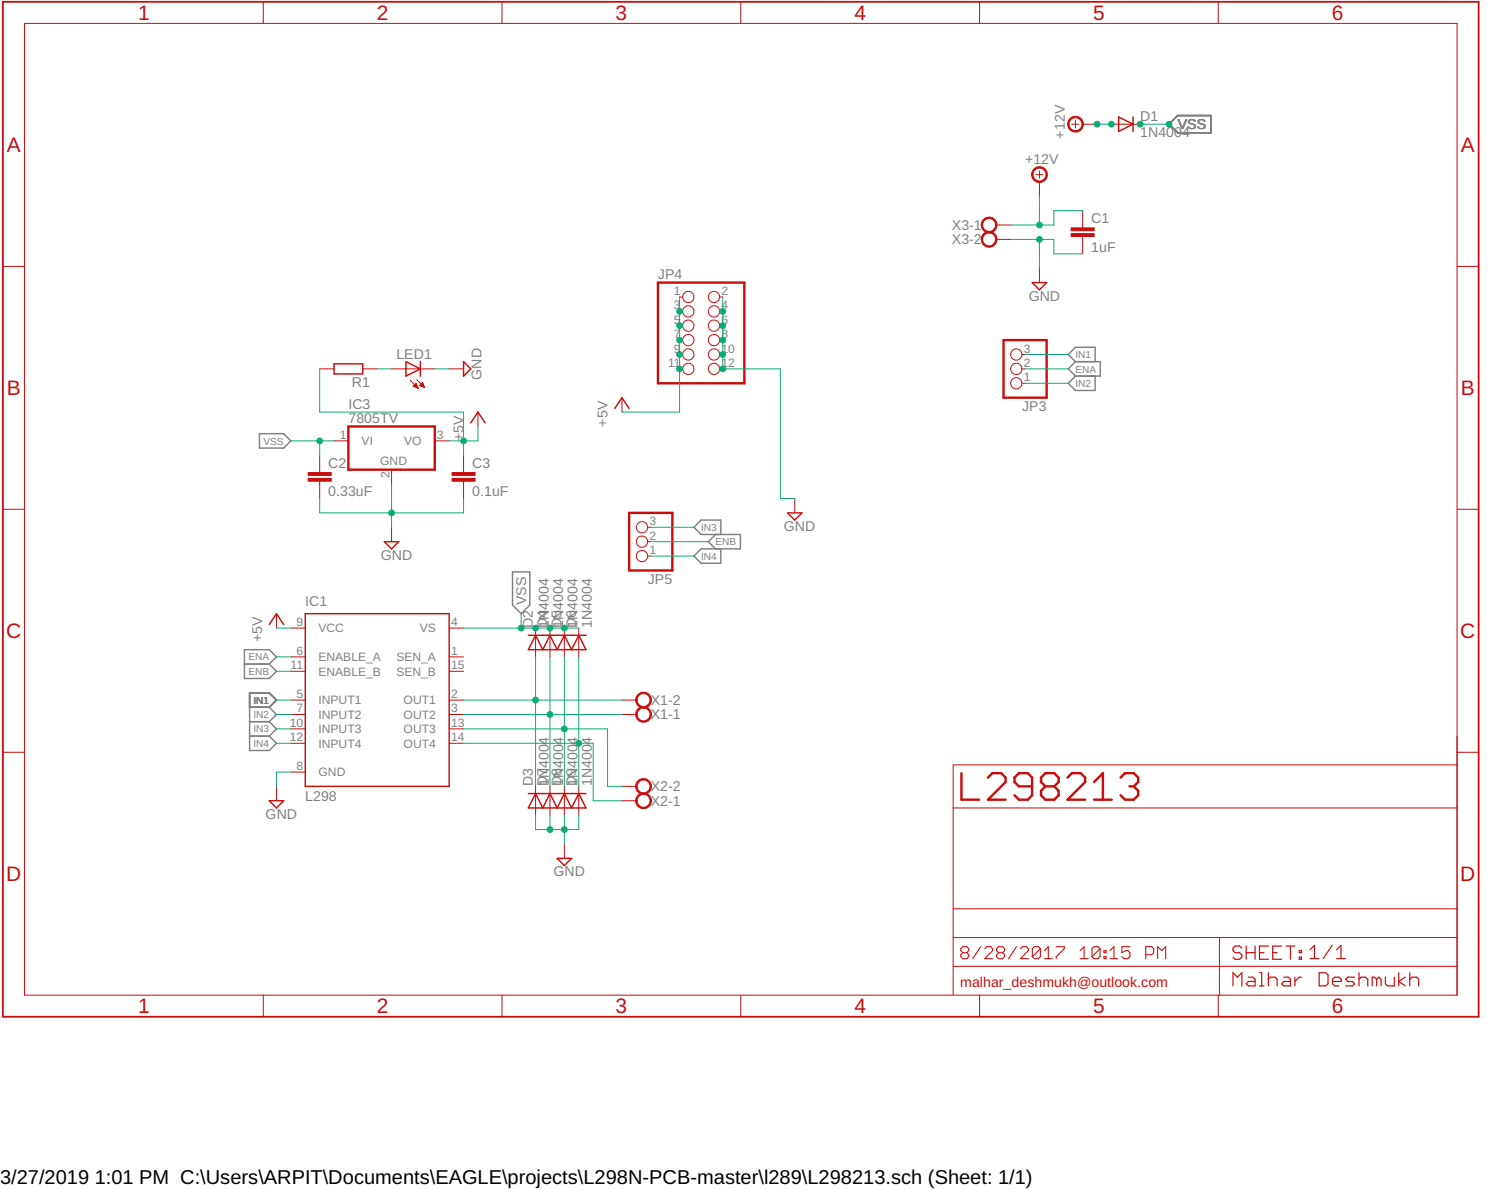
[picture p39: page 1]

3/27/2019 1:01 PM C:\Users\ARPIT\Documents\EAGLE\projects\L298N-PCB-master\l289\L298213.sch (Sheet: 1/1)

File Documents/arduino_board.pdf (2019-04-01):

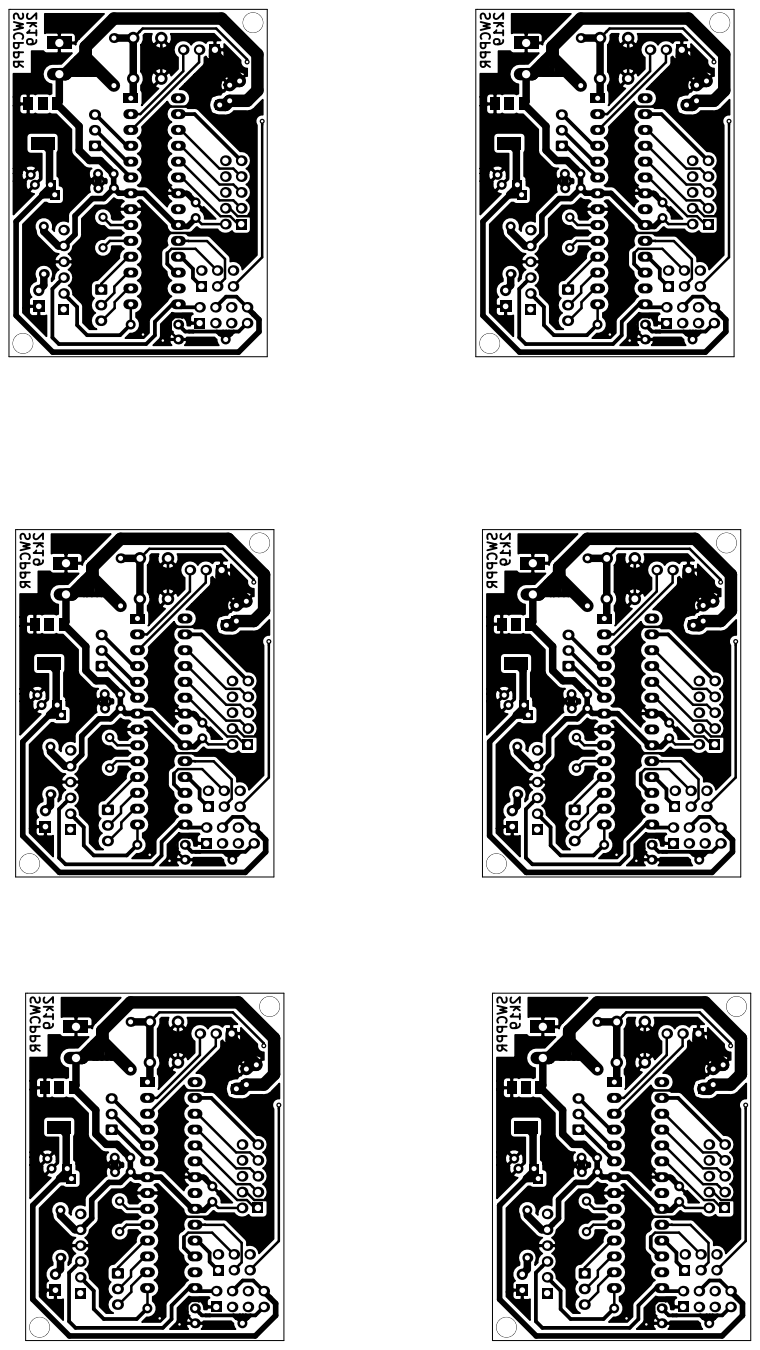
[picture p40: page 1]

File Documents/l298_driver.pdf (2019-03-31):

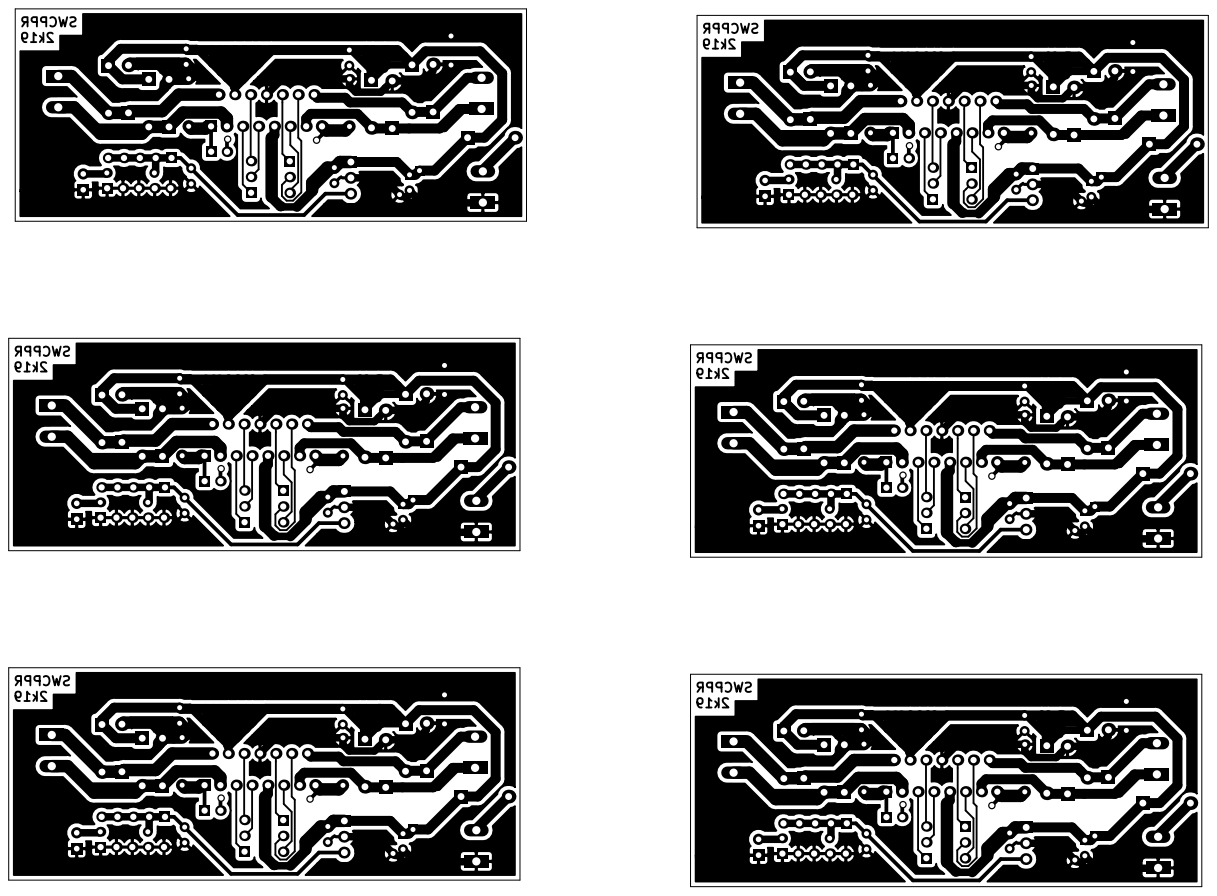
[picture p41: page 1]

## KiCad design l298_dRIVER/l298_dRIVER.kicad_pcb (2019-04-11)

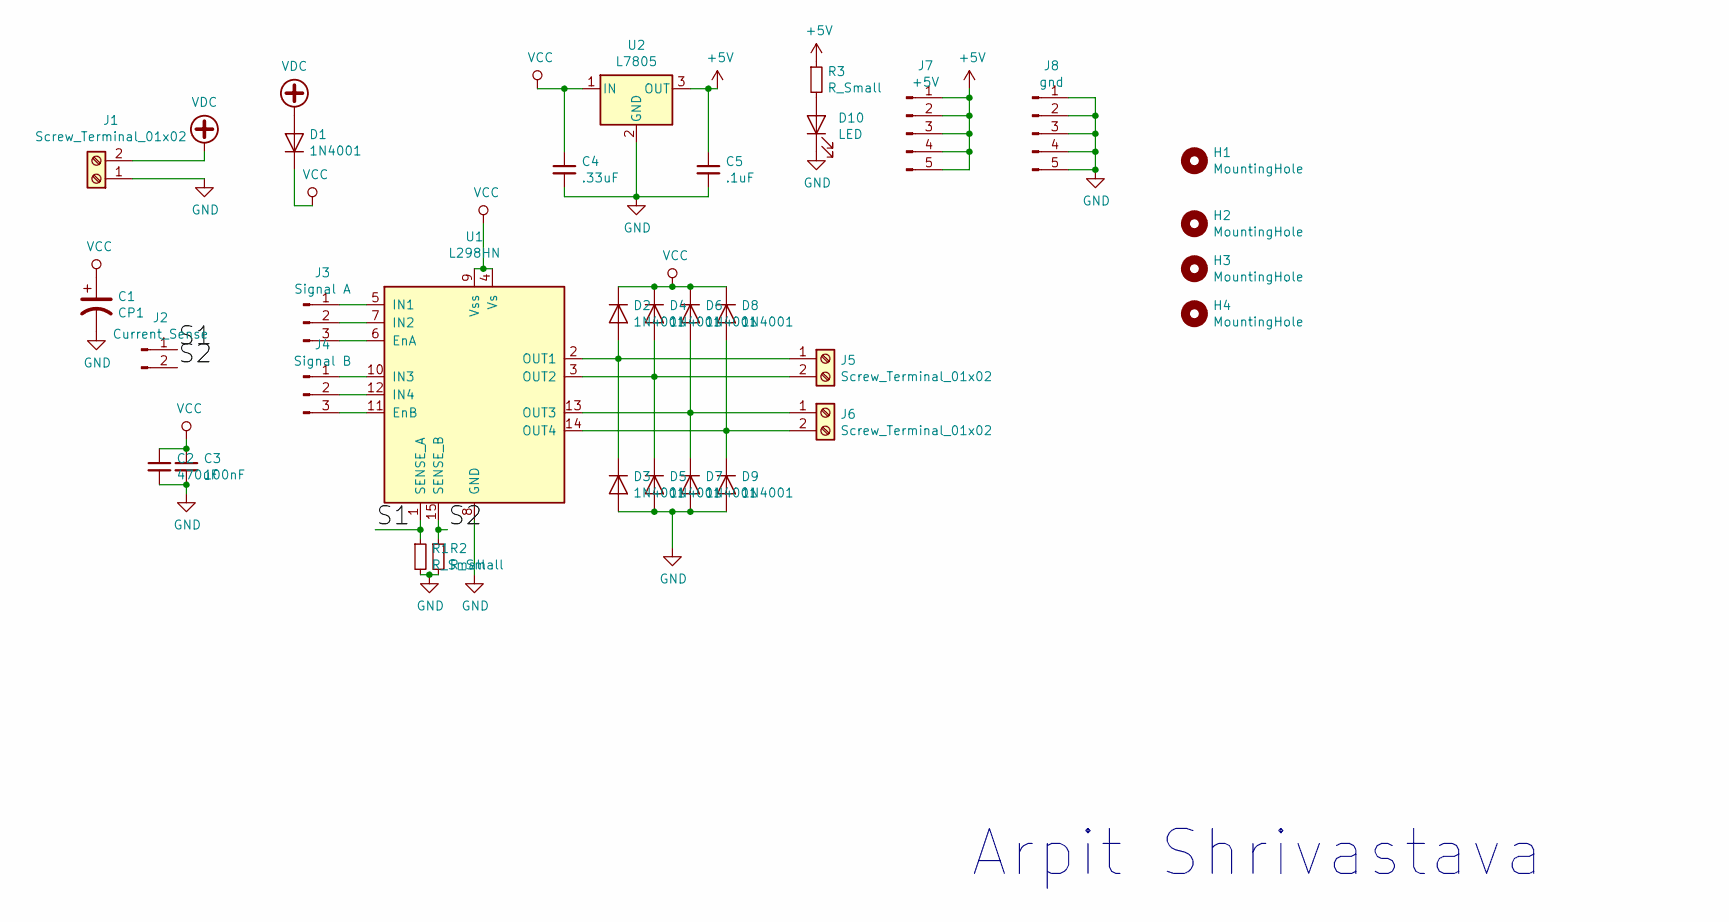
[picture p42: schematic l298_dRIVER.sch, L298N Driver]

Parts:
C1: CP1; CP_Radial_D10.0mm_P2.50mm_P5.00mm
C2: 470uF; C_Disc_D3.4mm_W2.1mm_P2.50mm
C3: 100nF; C_Disc_D3.4mm_W2.1mm_P2.50mm
C4: .33uF; C_Disc_D3.4mm_W2.1mm_P2.50mm
C5: .1uF; C_Disc_D3.4mm_W2.1mm_P2.50mm
D1, D2, D3, D4, D5, D6, D7, D8, D9: 1N4001; D_DO-41_SOD81_P7.62mm_Horizontal
D10: LED; LED_D3.0mm
H1, H2, H3, H4: MountingHole; MountingHole_3.2mm_M3_DIN965
J1, J5, J6: Screw_Terminal_01x02; TerminalBlock_Altech_AK300-2_P5.00mm
J2: Current_Sense; PinHeader_1x02_P2.54mm_Vertical
J3: Signal A; PinHeader_1x03_P2.54mm_Vertical
J4: Signal B; PinHeader_1x03_P2.54mm_Vertical
J7: +5V; PinHeader_1x05_P2.54mm_Vertical
J8: gnd; PinHeader_1x05_P2.54mm_Vertical
R1, R2, R3: R_Small; R_Axial_DIN0207_L6.3mm_D2.5mm_P7.62mm_Horizontal
U1: L298HN; TO-220-15_P2.54x2.54mm_StaggerOdd_Lead4.58mm_Vertical
U2: L7805; TO-220-3_Vertical

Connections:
+5V: C5.1, J7.1, J7.2, J7.3, J7.4, J7.5, R3.1, U2.3 (OUT)
/S1: J2.1, R1.1, U1.1 (SENSE_A)
/S2: J2.2, R2.1, U1.15 (SENSE_B)
GND: C1.2, C2.2, C3.2, C4.2, C5.2, D3.2 (A), D5.2 (A), D7.2 (A), D9.2 (A), D10.1 (K), J1.1, J8.1, J8.2, J8.3, J8.4, J8.5, R1.2, R2.2, U1.8 (GND), U2.2 (GND)
unnamed: D2.2 (A), D3.1 (K), J5.1, U1.2 (OUT1)
unnamed: D4.2 (A), D5.1 (K), J5.2, U1.3 (OUT2)
unnamed: D6.2 (A), D7.1 (K), J6.1, U1.13 (OUT3)
unnamed: D8.2 (A), D9.1 (K), J6.2, U1.14 (OUT4)
unnamed: D10.2 (A), R3.2
unnamed: J3.1, U1.5 (IN1)
unnamed: J3.2, U1.7 (IN2)
unnamed: J3.3, U1.6 (EnA)
unnamed: J4.1, U1.10 (IN3)
unnamed: J4.2, U1.12 (IN4)
unnamed: J4.3, U1.11 (EnB)
VCC: C1.1, C2.1, C3.1, C4.1, D1.1 (K), D2.1 (K), D4.1 (K), D6.1 (K), D8.1 (K), U1.4 (Vs), U1.9 (Vss), U2.1 (IN)
VDC: D1.2 (A), J1.2

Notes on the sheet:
Arpit Shrivastava

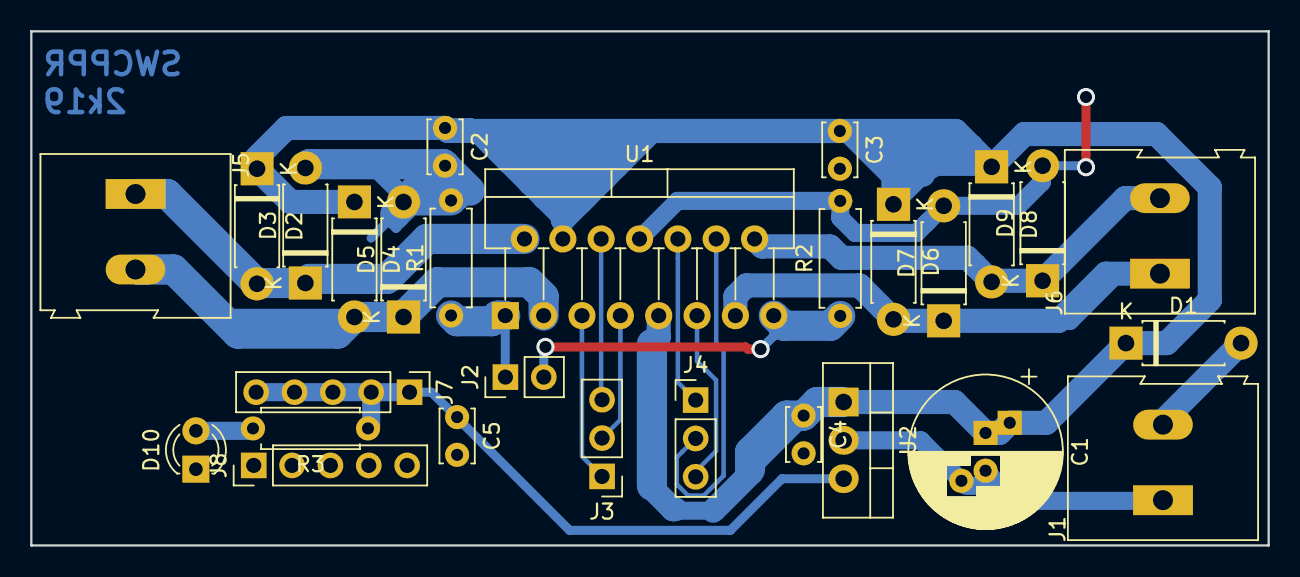
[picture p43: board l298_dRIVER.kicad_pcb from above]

Board: 2 copper layers, 82.0 x 34.1 mm, 32 parts (0 on the bottom side), 17 nets.

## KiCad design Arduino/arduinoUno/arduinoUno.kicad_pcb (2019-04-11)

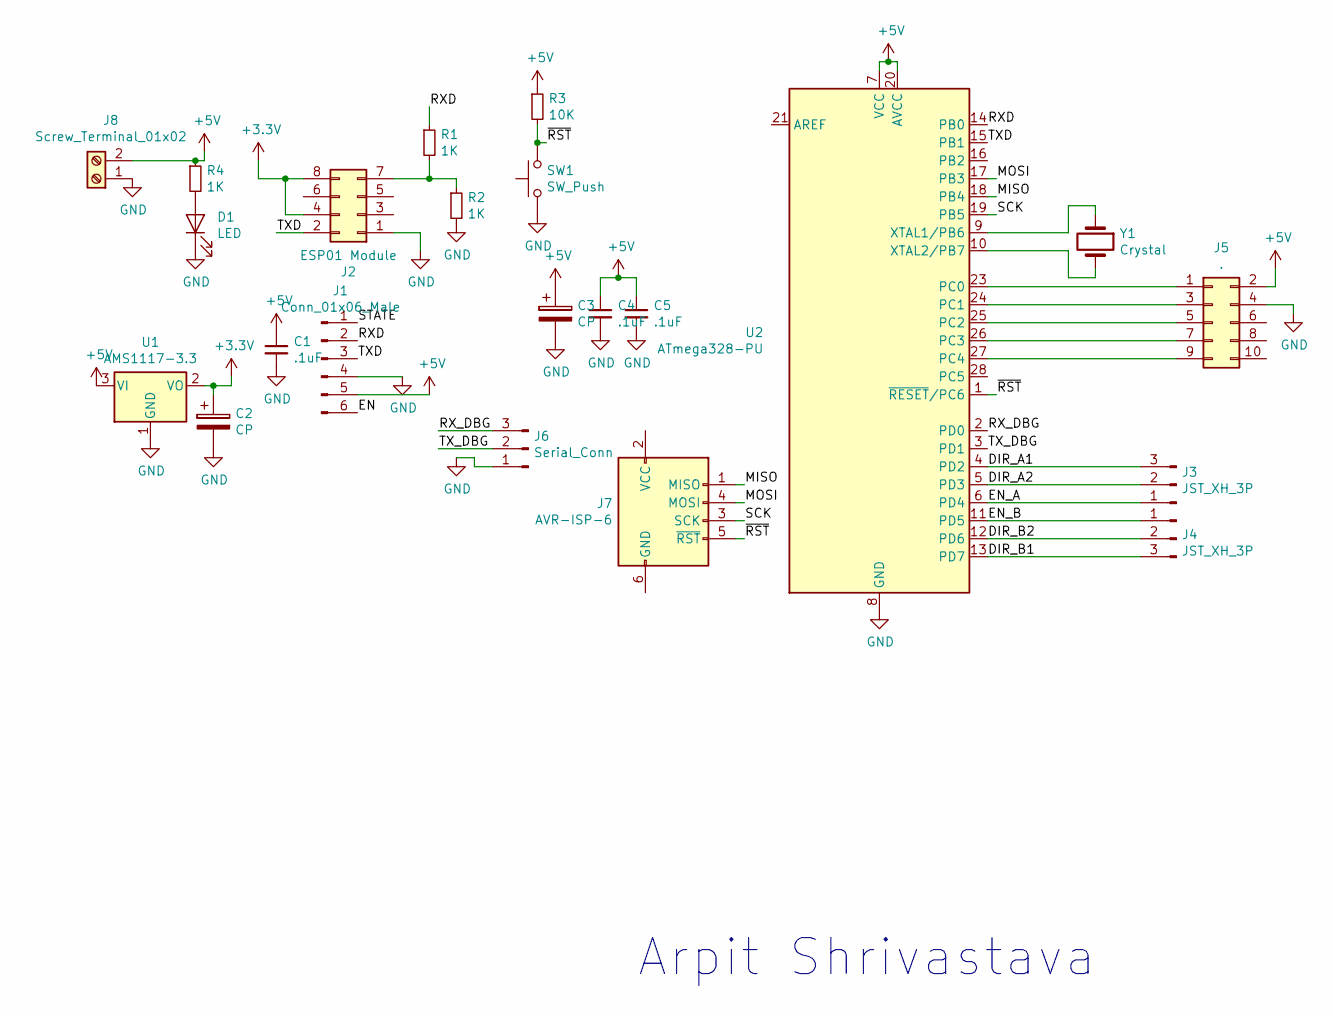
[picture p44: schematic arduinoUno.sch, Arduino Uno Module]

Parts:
C1, C4, C5: .1uF; C_Disc_D3.0mm_W1.6mm_P2.50mm
C2, C3: CP; CP_Radial_D10.0mm_P2.50mm_P5.00mm
D1: LED; LED_D3.0mm
J1: Conn_01x06_Male; PinSocket_1x06_P2.54mm_Vertical
J2: ESP01 Module; PinHeader_2x04_P2.54mm_Vertical
J3, J4: JST_XH_3P; JST_XH_B03B-XH-A_1x03_P2.50mm_Vertical
J5: .; IDC-Header_2x05_P2.54mm_Vertical
J6: Serial_Conn; PinHeader_1x03_P2.54mm_Vertical
J7: AVR-ISP-6; PinHeader_2x03_P2.54mm_Vertical
J8: Screw_Terminal_01x02; TerminalBlock_Altech_AK300-2_P5.00mm
R1, R2, R4: 1K; R_Axial_DIN0207_L6.3mm_D2.5mm_P7.62mm_Horizontal
R3: 10K; R_Axial_DIN0207_L6.3mm_D2.5mm_P7.62mm_Horizontal
SW1: SW_Push; SW_PUSH_6mm
U1: AMS1117-3.3; SOT-223-3_TabPin2
U2: ATmega328-PU; DIP-28_W7.62mm_Socket_LongPads
Y1: Crystal; Crystal_HC18-U_Vertical

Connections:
+3V3: C2.1, J2.4, J2.8, U1.2 (VO)
+5V: C1.1, C3.1, C4.1, C5.1, J1.5, J5.2, J8.2, R3.1, R4.1, U1.3 (VI), U2.7 (VCC), U2.20 (AVCC)
/DIR_A1: J3.3, U2.4 (PD2)
/DIR_A2: J3.2, U2.5 (PD3)
/DIR_B1: J4.3, U2.13 (PD7)
/DIR_B2: J4.2, U2.12 (PD6)
/EN: J1.6
/EN_A: J3.1, U2.6 (PD4)
/EN_B: J4.1, U2.11 (PD5)
/MISO: J7.1 (MISO), U2.18 (PB4)
/MOSI: J7.4 (MOSI), U2.17 (PB3)
/RXD: J1.2, R1.1, U2.14 (PB0)
/RX_DBG: J6.3, U2.2 (PD0)
/SCK: J7.3 (SCK), U2.19 (PB5)
/STATE: J1.1
/TXD: J1.3, J2.2, U2.15 (PB1)
/TX_DBG: J6.2, U2.3 (PD1)
/~RST: J7.5 (~RST), R3.2, SW1.2, U2.1 (~RESET~/PC6)
GND: C1.2, C2.2, C3.2, C4.2, C5.2, D1.1 (K), J1.4, J2.1, J5.4, J6.1, J8.1, R2.2, SW1.1, U1.1 (GND), U2.8 (GND), U2.22 (GND)
unnamed: D1.2 (A), R4.2
unnamed: J2.7, R1.2, R2.1
unnamed: J5.1, U2.23 (PC0)
unnamed: J5.3, U2.24 (PC1)
unnamed: J5.5, U2.25 (PC2)
unnamed: J5.7, U2.26 (PC3)
unnamed: J5.9, U2.27 (PC4)
unnamed: U2.9 (XTAL1/PB6), Y1.1
unnamed: U2.10 (XTAL2/PB7), Y1.2

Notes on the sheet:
Arpit Shrivastava

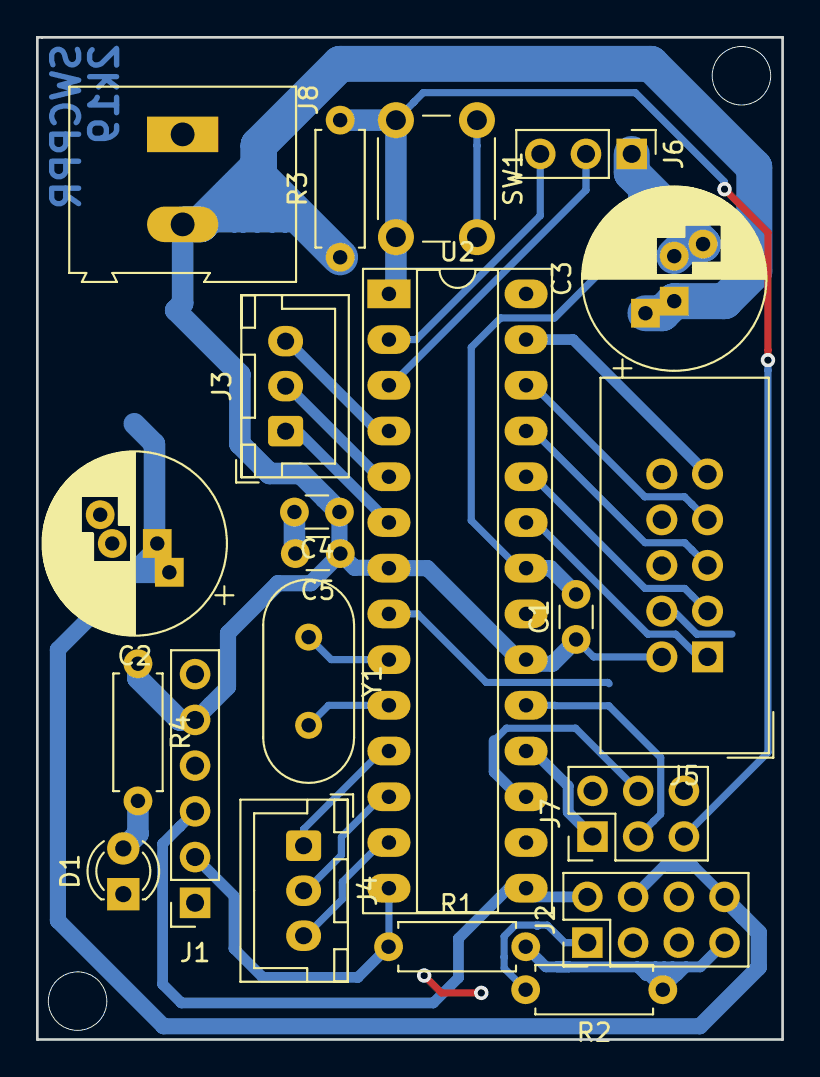
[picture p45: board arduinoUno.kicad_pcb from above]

Board: 2 copper layers, 41.4 x 55.7 mm, 22 parts (1 on the bottom side), 26 nets.

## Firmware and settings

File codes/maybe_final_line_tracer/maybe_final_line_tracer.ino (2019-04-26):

#define debug
//#define debug1
#define WANT
//#define pwm_high 210
//#define pwm_low 170
//#define pwm_least 140
//#define pwm_high 150
//#define pwm_low 110
//#define pwm_least 70
#define pwm_high 160
#define pwm_low 130
#define pwm_least 100
//const int mod1 = 8;
//const int mod2 = 9;
//const int mod3 = 10;
//const int mod4 = 11;
//const int mod5 = 12;
const int pwm_1 = 5;
const int pwm_2 = 6;
const int dir1PinA = 2;
const int dir1PinB = 3;
const int dir2PinA = 4;
const int dir2PinB = 7;


void serialprint()
{
  //  Serial.println(PINC, BIN);
  Serial.println("_______________________");
  //delay (400);
}


void backward()
{ digitalWrite(4, HIGH);
  digitalWrite(7, LOW );
  digitalWrite(2, HIGH );
  digitalWrite(3, LOW);
}


void forward()
{
  digitalWrite(4, LOW);
  digitalWrite(7, HIGH);
  digitalWrite(2, LOW );
  digitalWrite(3, HIGH);
}

void leftBack()
{
  digitalWrite(4, HIGH);
  digitalWrite(7, LOW);
  digitalWrite(2, LOW );
  digitalWrite(3, HIGH);
}

void rightBack()
{
  digitalWrite(4, LOW);
  digitalWrite(7, HIGH);
  digitalWrite(2, HIGH );
  digitalWrite(3, LOW);
}



////////////////////////////////////////////

unsigned long int val = 0b00000000;

void setup() {

  Serial.begin(9600);

  pinMode(pwm_1, OUTPUT);
  pinMode(pwm_2, OUTPUT);
  pinMode(dir1PinA, OUTPUT);
  pinMode(dir2PinA, OUTPUT);
  pinMode(dir1PinB, OUTPUT);
  pinMode(dir2PinB, OUTPUT);
  DDRB = 0x00;

  delay(500);
}

void loop() {

  uint8_t val = PINC;
  val = (PINC | 0b00100000);

#ifdef debug
  Serial.println(val, BIN);
  serialprint();
#endif

  switch (val)
  {
    //////////////////////////
    case 0b00110001 : {                   //centre
        analogWrite(pwm_1, pwm_high);
        analogWrite(pwm_2, pwm_high);
        forward();
      };
#ifdef WANT
      Serial.println("FORWARD");
#endif

      break;
    ////////////////////////
    case 0b00111001 :  {                   //soft right
        analogWrite(pwm_1, pwm_low);
        analogWrite(pwm_2, (pwm_high + 10));
        forward();
      };
#ifdef WANT
      Serial.println("SRight");
#endif
      break;

    ///////////////////////////
    case 0b00111000  :                              //right turn1
      while (val != 0b00111111 )
      {
        val = (PINC | 0b00100000);
        analogWrite(pwm_1, pwm_low);
        analogWrite(pwm_2, pwm_low);
        forward();
        Serial.println("inside till all white");
      }
      while (val != 0b00111001 )
      { val = (PINC | 0b00100000);
        {
          analogWrite(pwm_1, pwm_high);
          analogWrite(pwm_2, pwm_high);
          rightBack();
          Serial.println("inside till all centre1");
        }
      }
      while (val != 0b00110001 )
      { val = (PINC | 0b00100000);
        {
          analogWrite(pwm_1, pwm_high);
          analogWrite(pwm_2, pwm_high);
          rightBack();
          Serial.println("inside till all centre2");
        }
      }
#ifdef WANT
      Serial.println("hright");
#endif
      break;
    /////////////////////////////
    case 0b00111100  : {                                  //rightback
        analogWrite(pwm_1, pwm_high);
        analogWrite(pwm_2, pwm_high);
        rightBack();
      };
#ifdef WANT
      Serial.println("Hright");
#endif
      break;
    ////////////////////////////////
    case 0b00111110 : {                               //rightback
        analogWrite(pwm_1, pwm_high);
        analogWrite(pwm_2, pwm_high);
        rightBack();
      };
#ifdef WANT
      Serial.println("hright");
#endif
      break;
    ////////////////////////////////
    case 0b00111101 : {                               //rightback
        analogWrite(pwm_1, pwm_high);
        analogWrite(pwm_2, pwm_high);
        rightBack();
      };
#ifdef WANT
      Serial.println("hright");
#endif
      break;
    ///////////////////////////////
    case 0b00110000 :                             //right turn 2.
      while (val != 0b00111111 )
      {
        val = (PINC | 0b00100000);
        analogWrite(pwm_1, pwm_low);
        analogWrite(pwm_2, pwm_low);
        forward();
        Serial.println("inside till all white");
      }
      while (val != 0b00111001 )
      { val = (PINC | 0b00100000);
        {
          analogWrite(pwm_1, pwm_high);
          analogWrite(pwm_2, pwm_high);
          rightBack();
          Serial.println("inside till all centre1");
        }
      }
      while (val != 0b00110001 )
      { val = (PINC | 0b00100000);
        {
          analogWrite(pwm_1, pwm_high);
          analogWrite(pwm_2, pwm_high);
          rightBack();
          Serial.println("inside till all centre2");
        }
      }

#ifdef WANT
      Serial.println("HARD Right");
#endif
      break;

    ////////////////////////////////////        //left codes

    case 0b00110011 : {                       //soft left
        analogWrite(pwm_1, pwm_high);
        analogWrite(pwm_2, pwm_low);
        forward();
      };
#ifdef WANT
      Serial.println("sleft");
#endif
      break;
    //////////////////////////////////
    case 0b00100011  :                         //left turn
      while (val != 0b00111111 )
      {
        val = (PINC | 0b00100000);
        analogWrite(pwm_1, pwm_low);
        analogWrite(pwm_2, pwm_low);
        forward();
        Serial.println("inside till all white");
      }
      while (val != 0b00110011 )
      { val = (PINC | 0b00100000);
        {
          analogWrite(pwm_1, pwm_high);
          analogWrite(pwm_2, pwm_high);
          leftBack();
          Serial.println("inside till all centre1");
        }
      }
      while (val != 0b00110001 )
      { val = (PINC | 0b00100000);
        {
          analogWrite(pwm_1, pwm_high);
          analogWrite(pwm_2, pwm_high);
          leftBack();
          Serial.println("inside till all centre2");
        }
      }
#ifdef WANT
      Serial.println("hleft");
#endif
      break;

    //////////////////////////////////
    case 0b00100111 : {                       //leftback
        analogWrite(pwm_2, pwm_low);
        analogWrite(pwm_1, pwm_high);
        leftBack();
      };
#ifdef WANT
      Serial.println("hleft");
#endif
      break;
    //////////////////////////////////
    case 0b00101111 : {                       //leftback
        analogWrite(pwm_1, pwm_high);
        analogWrite(pwm_2, pwm_low);
        leftBack();
      };
#ifdef WANT
      Serial.println("sleft");
#endif
      break;
    //////////////////////////////////
    case 0b00110111 : {                     //leftback
        analogWrite(pwm_1, pwm_high);
        analogWrite(pwm_2, pwm_low);
        leftBack();
      };
#ifdef WANT
      Serial.println("sleft");
#endif
      break;
    //////////////////////////////////

    case 0b00100001 :                       //left turn
      while (val != 0b00111111 )
      {
        val = (PINC | 0b00100000);
        analogWrite(pwm_1, pwm_low);
        analogWrite(pwm_2, pwm_low);
        forward();
        Serial.println("inside till all white");
      }
      while (val != 0b00110011 )
      { val = (PINC | 0b00100000);
        {
          analogWrite(pwm_1, pwm_high);
          analogWrite(pwm_2, pwm_high);
          leftBack();
          Serial.println("inside till all centre1");
        }
      }
      while (val != 0b00110001 )
      { val = (PINC | 0b00100000);
        {
          analogWrite(pwm_1, pwm_high);
          analogWrite(pwm_2, pwm_high);
          leftBack();
          Serial.println("inside till all centre2");
        }
      }
#ifdef WANT
      Serial.println("hleft");
#endif
      break;
    //////////////////////////////////
    case 0b00100000 : {
        analogWrite(pwm_1, pwm_low);
        analogWrite(pwm_2, pwm_low);
        forward();
      };
#ifdef WANT
      Serial.println("ALL UNDER BLACK");
#endif
      break;
    //////////////////////////////////
    default: {
        analogWrite(pwm_1, pwm_low);
        analogWrite(pwm_2, pwm_low);
        forward();
      };
#ifdef WANT
      Serial.println("Default");
#endif
      /////////////////////////////////
      delay(0);
  }
}

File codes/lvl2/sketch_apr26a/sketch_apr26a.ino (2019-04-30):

#include"Bluetooth.h"
//#include"ServoCode.h"


#include <Servo.h>
Servo myservo;
int pos1 = 0;

#define debug
//#define debug1
#define WANT
//#define pwm_high 210
//#define pwm_low 170
//#define pwm_least 140
#define pwm_high 160
#define pwm_low 120
#define pwm_least 70
const int pwm_1 = 5;
const int pwm_2 = 6;
const int dir1PinA = 2;
const int dir1PinB = 3;
const int dir2PinA = 4;
const int dir2PinB = 7;
const int IR = 12;
boolean go = 1;
boolean done = 0;
boolean flag = 0;
boolean Tflag = 0;
boolean Rflag = 0;
boolean Lflag = 0;
boolean blackflag = 0;
boolean Sourceflag = 0;
boolean Destinationflag = 0;
boolean runflag = 0;
int jnCount = 0;
int count = 0;
/////
boolean gotData = 0;
boolean data = 0;
int Sourcedata = 0;
int Destinationdata = 0;
/////
unsigned long int val = 0b00000000;




void serialprint()
{
  //  Serial.println(PINC, BIN);
  Serial.println("_______________________");
  //delay (400);
}


void backward()
{ digitalWrite(4, HIGH);
  digitalWrite(7, LOW );
  digitalWrite(2, HIGH );
  digitalWrite(3, LOW);
}


void forward()
{
  digitalWrite(4, LOW);
  digitalWrite(7, HIGH);
  digitalWrite(2, LOW );
  digitalWrite(3, HIGH);
}

void leftBack()
{
  digitalWrite(4, HIGH);
  digitalWrite(7, LOW);
  digitalWrite(2, LOW );
  digitalWrite(3, HIGH);
}

void rightBack()
{
  digitalWrite(4, LOW);
  digitalWrite(7, HIGH);
  digitalWrite(2, HIGH );
  digitalWrite(3, LOW);
}
void Stop()
{
  digitalWrite(4, LOW);
  digitalWrite(7, LOW);
  digitalWrite(2, LOW );
  digitalWrite(3, LOW);
}

////////////////////////////////////////////
void ModLeft()
{
  Serial.println("INSIDE MOD LEFT ");
  while (val != 0b00111000)
  {
    val = (PINC | 0b00100000);
    analogWrite(pwm_1, pwm_high);
    analogWrite(pwm_2, pwm_high);
    leftBack();
    Serial.println("inside till left IR on LINE");
  }
  while (val != 0b00110011 )
  {
    val = (PINC | 0b00100000);
    analogWrite(pwm_1, pwm_high);
    analogWrite(pwm_2, pwm_high);
    leftBack();
    Serial.println("inside till all centre1");
  }
  while (val != 0b00110001 )
  { val = (PINC | 0b00100000);
    analogWrite(pwm_1, pwm_high);
    analogWrite(pwm_2, pwm_high);
    leftBack();
    Serial.println("inside till all centre2");
  }
}
////////////////////////////////////////////
void ModRight()
{
  Serial.println("INSIDE MOD Right ");
  while (val != 0b00100011)
  {
    val = (PINC | 0b00100000);
    analogWrite(pwm_1, pwm_high);
    analogWrite(pwm_2, pwm_high);
    rightBack();
    Serial.println("inside till right IR on LINE");
  }
  while (val != 0b00111001 )
  {
    val = (PINC | 0b00100000);
    analogWrite(pwm_1, pwm_high);
    analogWrite(pwm_2, pwm_high);
    rightBack();
    Serial.println("inside till all centre1");
  }
  while (val != 0b00110001 )
  { val = (PINC | 0b00100000);
    analogWrite(pwm_1, pwm_high);
    analogWrite(pwm_2, pwm_high);
    rightBack();
    Serial.println("inside till all centre2");
  }
}

void make180()
{
  while (val != 0b00111001 )
  {
    val = (PINC | 0b00100000);
    analogWrite(pwm_1, pwm_high);
    analogWrite(pwm_2, pwm_high);
    leftBack();
    Serial.println("inside till all centre1");
  }
  while (val != 0b00110001 )
  { val = (PINC | 0b00100000);
    analogWrite(pwm_1, pwm_high);
    analogWrite(pwm_2, pwm_high);
    leftBack();
    Serial.println("inside till all centre2");
  }
}
//////////////////////////////servo///////////////
void sod()
{
  myservo.attach(11);
  delay(100);
  Serial.println("SOD");

  for (pos1 = 122; pos1 >= 45; pos1 -= 2)
  {
    Serial.println(pos1);
    myservo.write(pos1);
    delay(50);
  }
}
/////////////////
void pakad()
{
  myservo.attach(11);
  delay(100);
  Serial.println("PAKAD");
  for (pos1 = 45; pos1 <= 122; pos1 += 2)
  {
    Serial.println(pos1);
    myservo.write(pos1);
    delay(50);
  }
}
//////////////////////////////////////////


void setup() {

  Serial.begin(9600);
  myservo.attach(11);

  pinMode(pwm_1, OUTPUT);
  pinMode(pwm_2, OUTPUT);
  pinMode(dir1PinA, OUTPUT);
  pinMode(dir2PinA, OUTPUT);
  pinMode(dir1PinB, OUTPUT);
  pinMode(dir2PinB, OUTPUT);
  pinMode(IR, OUTPUT);
  DDRB = 0x00;
  mySerial.begin(9600);
  mySerial.println("welcome ");
  sod();

  delay(500);
}

void loop()
{

  while (Sourceflag != 1)
  {
    mySerial.println("Enter Source data....");
    delay(500);
    Sourceflag = 0;
    Sourcedata = 0;
    Serial.println("Getting Source Data over BLE.");
    Sourcedata = getData();
    delay(100);
    if (Sourcedata > 0)
    {
      Serial.print("Received Data:  "); Serial.println(Sourcedata);
      Sourceflag = 1;
      gotData = 0;
    }
    data = 0;
  }
  while (Destinationflag != 1)
  {
    mySerial.println("Enter Destination data....");
    delay(500);
    Destinationdata = 0;
    Destinationflag = 0;
    Serial.println("Getting Destination Data over BLE.");
    Destinationdata = getData();
    delay(100);
    if (Destinationdata > 0)
    {
      Serial.print("Received Data:  "); Serial.println(Destinationdata);
      Destinationflag = 1;
      gotData = 1;
    }
    Serial.print("Source Data:  "); Serial.println(Sourcedata);
    Serial.print("Destination Data:  "); Serial.println(Destinationdata);
    delay(2000);
  }

  if (Sourceflag & Destinationflag == 1)
    data = 1;

  //  if (go == 1)                          //
  //  {
  //    Tflag = Sourcedata % 2;
  //  }
  //  else
  //  {
  //    if (Destinationdata > Sourcedata)
  //      Tflag = Destinationdata % 2;
  //    else
  //      Tflag != (Destinationdata % 2);
  //  }

  uint8_t val = PINC;
  val = (PINC | 0b00100000);
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

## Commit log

2019-03-31 added sample report
2019-04-01 added Uno board
2019-04-09 Boards Aded
    [arduinoUno.kicad_pcb, arduinoUno.sch, l298_dRIVER.kicad_pcb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]
2019-04-21 stepper test code
2019-04-23 PDF FOR PRINTING ADDED
2019-04-24 Motor driver cmp
2019-04-24 datatsheet motor
